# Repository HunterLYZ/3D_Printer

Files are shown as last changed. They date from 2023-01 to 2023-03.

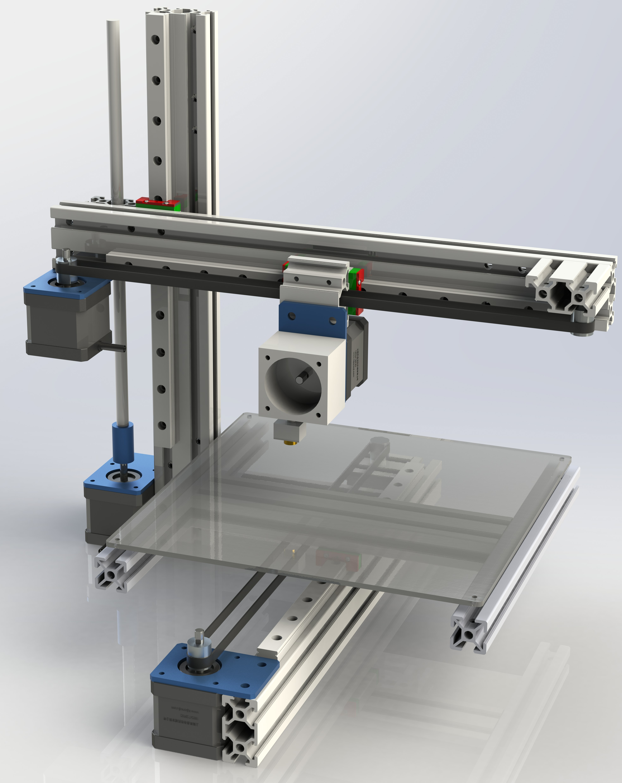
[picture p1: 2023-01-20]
images/1.JPG

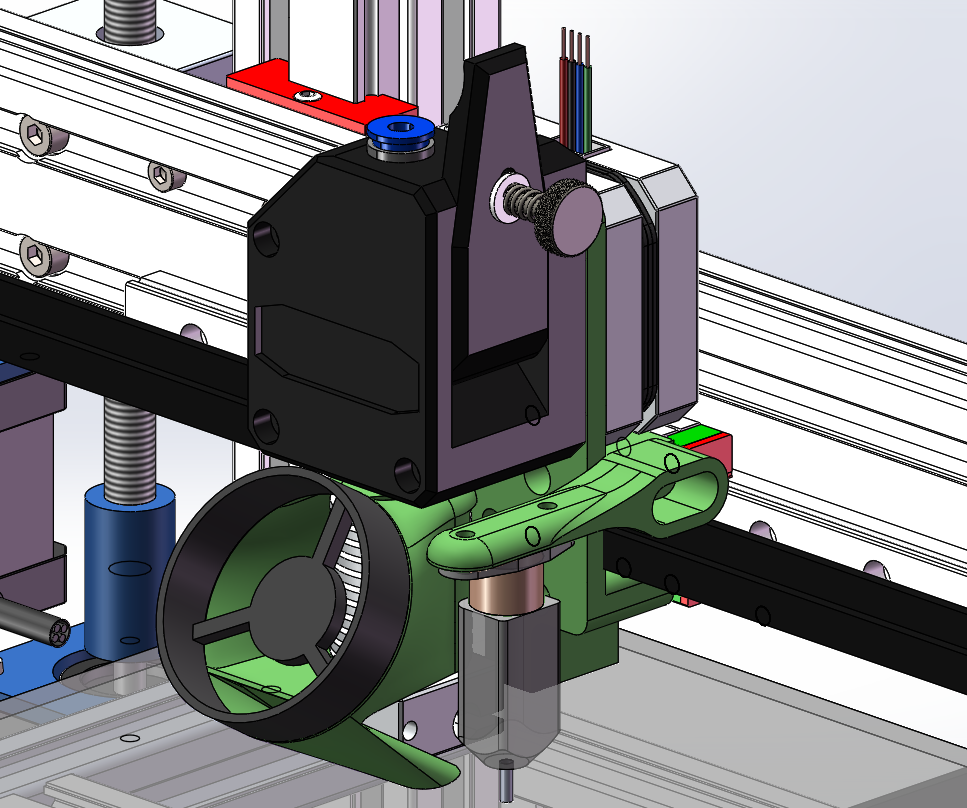
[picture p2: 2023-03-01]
3dtouch BedLeveling/屏幕截图 2023-03-01 191434.png

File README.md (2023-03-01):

# 3D_Printer

Mostly Aluminum Extrusion 3D Printer without printed part and laser cut；

Aim to use the simplest parts to create a low cost 3D printer！

Video description：【DIY悬臂3D打印机，低成本全金属方案开源】 https://www.bilibili.com/video/BV1WG4y1X7HM/?share_source=copy_web&vd_source=848a0bdee68da7365b0da106937491c6
fullview

A simple fan duct for better overhangs：

https://www.thingiverse.com/thing:5817219

屏幕截图 2023-03-01 191434

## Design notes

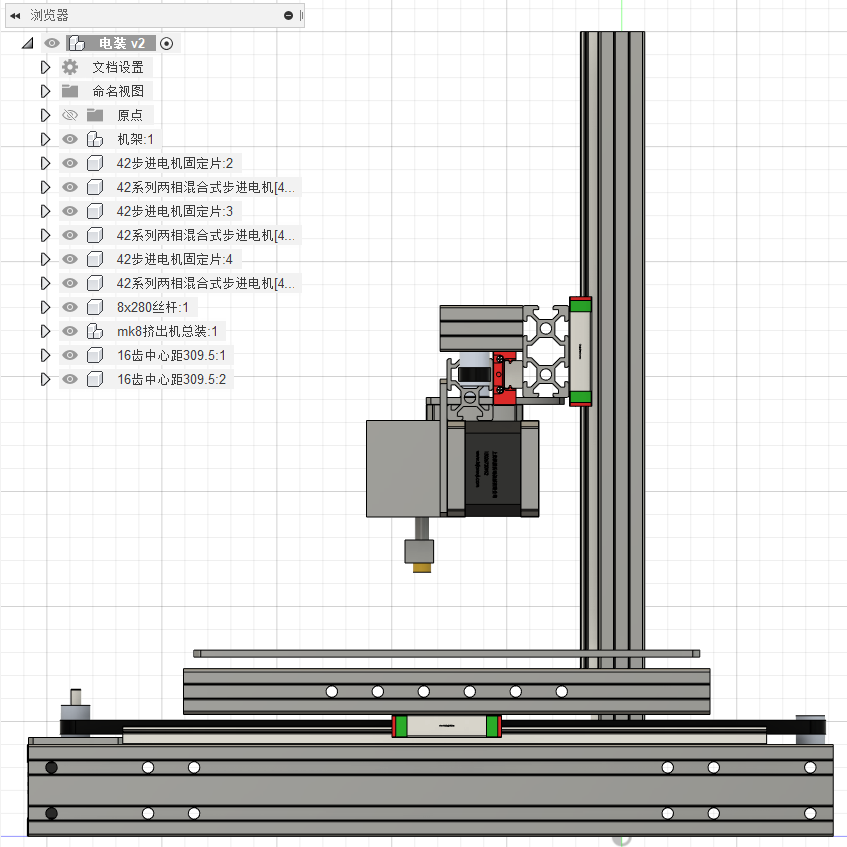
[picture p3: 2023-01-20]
images/右.png

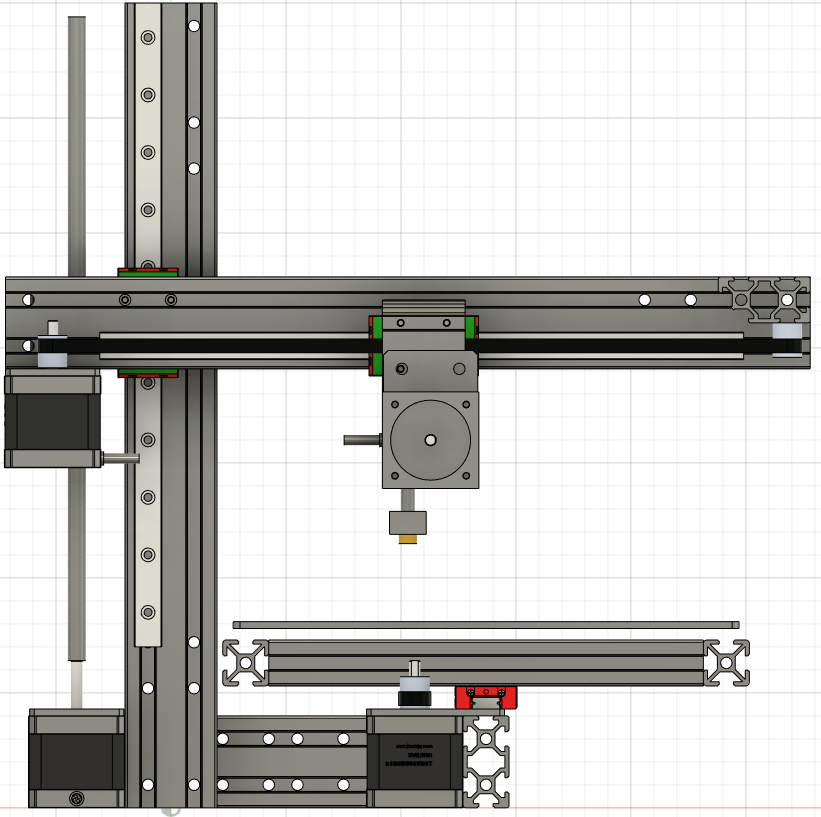
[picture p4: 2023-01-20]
images/前.png

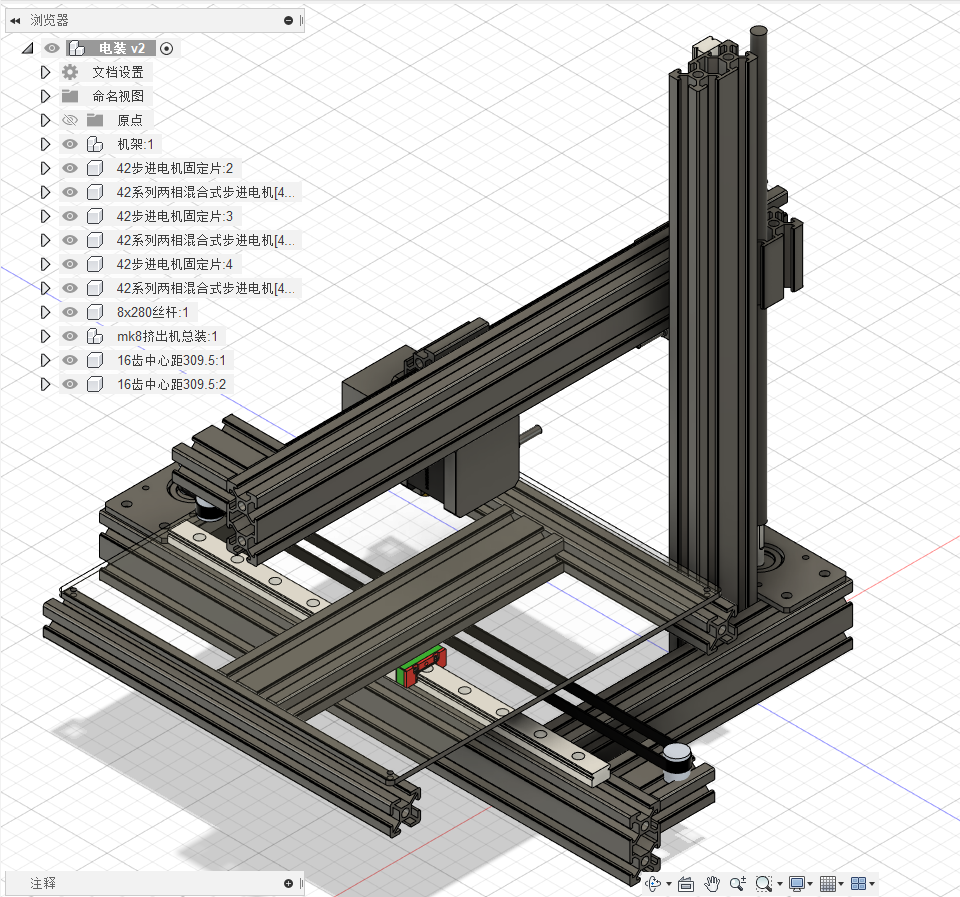
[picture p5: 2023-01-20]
images/侧后.png

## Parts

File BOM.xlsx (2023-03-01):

序号 |  | 名称 | 规格 | 数量 | 单价 | 运费 | 总价 | 链接 | 备注
 | 线轨 | 线轨 | 270mm长轨道+12H滑块（轻预压） | 3 | 30 | 10 | 100 | 闲鱼拆机线轨 | 除非有相关经验，否则建议买新的
 | 铝型材 | 欧标2040V 铝型材 | 360mm长 参照图纸加工 | 2 | 9.83 | 12 | 31.66 | TDT欧标铝型材2020拼装diy框架工作台配件工业框架2020铝合金型材-淘宝网 (taobao.com) (https://item.taobao.com/item.htm?spm=a1z1r.7974869.0.0.269c3ad4cUHl1e&id=610844048816)
 |  |  | 189mm长 参照图纸加工 | 2 | 5.15 | 0 | 10.3
 |  |  | 380mm长 无需加工 | 1 | 10.37 | 0 | 10.37
 |  |  | 40mm长 参照图纸加工 | 3 | 1.07 | 0 | 3.21
 |  | 欧标2020 铝型材 | 228.5mm长 无需加工 | 2 | 3.36 | 0 | 6.72
 | 步进电机 | 挤出机步进电机 | 带1米XH2.54配线高23mm | 1 | 11.4 | 0 | 11.4 | 3D打印机配件42步进电机泰坦挤出机电机小型微型写字机雕刻机马达-淘宝网 (taobao.com) (https://item.taobao.com/item.htm?spm=a1z09.2.0.0.7cb62e8dnEPceC&id=669131789105&_u=1208rr7usgf1c7) | 挤出机用，不超过28mm
 |  | 步进电机 | 40mm高 | 3 | 18 | 6 | 60 | 项目剩余，仅估价
 |  | 42步进电机固定片 | 银色*2；黑色*2共4个 | 4 | 3 | 0 | 12 | 3D打印机配件 42步进电机固定片 安装支架 适用2020 2040铝型材-淘宝网 (taobao.com) (https://item.taobao.com/item.htm?spm=a1z09.2.0.0.7cb62e8dnEPceC&id=595525201976&_u=1208rr7usge8b5)
 |  | 电机线 | 双头白色段子（500mm） | 1 | 0.7 | 0 | 0.7 | XH2.54端子电机线 杜邦头 3D打印机配件 步进电机链接线4pin-6pin-淘宝网 (taobao.com) (https://item.taobao.com/item.htm?spm=a1z10.3-c-s.w4002-17331600343.27.22cc3e69DtHcDt&id=560493265538)
 |  |  | 双头白色段子（800mm） | 1 | 0.9 | 0 | 0.9
 |  |  | 双头白色段子（1000mm） | 1 | 1.1 | 0 | 1.1
 | 同步带轮 | 同步轮 | 20齿内孔5带宽6 | 2 | 1.18 | 0 | 2.36 | 3D打印机2GT同步轮 16/20/40齿传动皮带轮步进电机主动轮带宽6/10-淘宝网 (taobao.com) (https://item.taobao.com/item.htm?spm=a1z10.3-c-s.w4002-17331600343.12.72ce3e69ifWSzl&id=559194333476)
 |  | 惰轮 | 20齿内孔3 带宽6带齿 | 2 | 2.03 | 0 | 4.06 | 3D打印机2GT惰轮 同步带惰轮皮带轮H型被动滑轮16/20齿带宽6/10mm-淘宝网 (taobao.com) (https://item.taobao.com/item.htm?spm=a1z0d.6639537/tb.1997196601.4.631b7484anwYdu&id=559682437946)
 |  | 同步带 | GT2-6mm 1米 | 2 | 1.35 | 0 | 2.7 | 3D打印机2GT同步带 高品质橡胶PU钢丝 GT2传动开口皮带带宽6/10mm-淘宝网 (taobao.com) (https://item.taobao.com/item.htm?spm=a1z10.3-c-s.w4002-17331600343.17.22cc3e69DtHcDt&id=558903222636)
 |  | 同步带固定片 | 夹压带铝齿片 9*40mm | 1 | 0.7 | 0 | 0.7 | Reprap 3D打印机 同步带固定片夹压带铝齿片 9*40mm 氧化处理-淘宝网 (taobao.com) (https://item.taobao.com/item.htm?spm=a1z10.3-c-s.w4002-17331600343.31.22cc3e69DtHcDt&id=560377410082)
 | 热床 | 铝基板热床 | 220*220 | 1 | 25 | 0 | 25 | 3D打印机热床 MK3铝基板热床平台 加热床 reprap标准 220*220*3mm-淘宝网 (taobao.com) (https://item.taobao.com/item.htm?id=561067851671)
 |  | 钢化玻璃板 | 220*220 | 1 | 10.3 | 0 | 10.3 | 3D打印机配件 MK2B加热热床玻璃平台高硼硅钢化玻璃板213x200x3mm-淘宝网 (taobao.com) (https://item.taobao.com/item.htm?spm=a1z10.3-c-s.w4002-17331600343.9.650e3e69Mw5PF8&id=556801926773)
 |  | 热床弹簧 | 挤出机强力弹簧 | 4 | 0.1 | 0 | 0.4 | 同拓3D打印机配件 挤出机强力弹簧 镀镍 wade/Ultimaker /Makerb-淘宝网 (taobao.com) (https://item.taobao.com/item.htm?spm=a1z10.3-c-s.w4002-17331600343.18.7d463e693q8sTS&id=559979934625)
 |  | 晶格玻璃夹 |  | 4 | 0.85 | 0 | 3.4 | 3d打印机晶格玻璃夹 不锈钢热床固定夹子Ender 3同款 可夹7mm-淘宝网 (taobao.com) (https://item.taobao.com/item.htm?spm=a1z10.3-c-s.w4002-17331600343.13.58433e69OT4IVv&id=643012602050)
 |  | NTC热敏电阻 | 银色一支 | 1 | 0.5 | 0 | 0.5 | 3D打印机 NTC热敏电阻 100K/100欧姆 配MK2a 1%高精度 传感器-淘宝网 (taobao.com) (https://item.taobao.com/item.htm?spm=a1z10.3-c-s.w4002-17331600343.45.4a173e69rOCZgU&id=560081231115)
 |  | 固体胶棒 |  | 1 | 2.2 | 0 | 2.2 | 3D打印机配件固体胶棒 防翘边固体胶水溶性PVP胶棒冷打防翘边胶棒-淘宝网 (taobao.com) (https://item.taobao.com/item.htm?spm=a230r.1.14.16.6d2f24e0IERJIc&id=648496928113&ns=1&abbucket=20)
 | 打印头 | 测温电阻NTC100K | 高温版350° | 1 | 2.1 | 0 | 2.1 | 同拓3D打印机测温电阻NTC100K热敏电阻传感器配件热头高温版350度-淘宝网 (taobao.com) (https://item.taobao.com/item.htm?spm=a1z10.3-c-s.w4002-17331600343.51.6fd93e69hTs6JR&id=575202356478)
 |  | 加热棒 | 12V60W 一米 | 1 | 7.5 | 0 | 7.5 | 高品质3D打印机 E3DV6挤出头热端加热棒6*20mm12V/24V 70W加热管-淘宝网 (taobao.com) (https://item.taobao.com/item.htm?spm=a1z10.3-c-s.w4002-17331600343.29.12a93e693xUKBs&id=680484241425)
 |  | 加热块 | 兼容pt1000 | 1 | 1.35 | 0 | 1.35 | 3D打印机配件 新款E3D-V6加热块 硅胶套 兼容PT100传感器加热铝块-淘宝网 (taobao.com) (https://item.taobao.com/item.htm?spm=a1z10.3-c-s.w4002-17331600343.17.6fd93e69hTs6JR&id=565058815432)
 |  | 喷嘴 | 0.4mm | 2 | 0.05 | 0 | 0.1 | 3D打印机喷头 E3D喷嘴V5V6 MK8黄铜带刻字 1.75/3.0耗材 M6螺纹-淘宝网 (taobao.com) (https://item.taobao.com/item.htm?spm=a1z10.3-c-s.w4002-17331600343.14.72ce3e69ifWSzl&id=559468438120)
 |  | 喉管 | TC4钛合金 | 1 | 5.65 | 0 | 5.65 | 3d打印机钛合金喉管e3d V6远程 TC4钛合金耐磨耐腐蚀高温耗材专用-淘宝网 (taobao.com) (https://item.taobao.com/item.htm?spm=a1z10.3-c-s.w4002-17331600343.36.6ee13e69zr7aBP&id=635261524077)
 |  | 散热管 | V6远程通用M7喉管 | 1 | 3.2 | 0 | 3.2 | 3d打印机配件 J-head散热管 E3D-V5 V6远程近程散热器片 1.75/3mm-淘宝网 (taobao.com) (https://item.taobao.com/item.htm?spm=a1z10.3-c-s.w4002-17331600343.47.50f73e69FBJrfH&id=559984859809)
 |  | 风扇 | v6风扇罩+12v风扇 | 1 | 4.8 | 0 | 4.8 | 3d打印机风扇罩 E3D V5 V6专用注塑散热器风扇支架固定座 30*30-淘宝网 (taobao.com) (https://item.taobao.com/item.htm?spm=a1z09.2.0.0.7cb62e8dnEPceC&id=559908577688&_u=1208rr7usgd1f7)
 | 挤出机 | 四氟管 | 2*4mm | 1 | 2 | 0 | 2 | 铁氟龙管聚四氟乙烯四氟管特氟龙PTFE软管耐腐蚀高温送料管导料管-淘宝网 (taobao.com) (https://item.taobao.com/item.htm?spm=a1z10.3-c-s.w4002-17331600343.35.11473e69qQkCo4&id=659862681620)
 |  | BMG挤出机 | 透明款 | 1 | 22 | 0 | 22 | 3D打印机配件 新款BMG透明挤出机 双齿轮减速 软性耗材远近程可用-淘宝网 (taobao.com) (https://item.taobao.com/item.htm?spm=a1z10.3-c-s.w4002-17331600343.31.749a3e69Eeaqys&id=640392766176)
 | 主板 | 2004显示屏 |  | 1 | 28 | 0 | 28 | 3d打印机显示屏模块 1.4主板智能控制器 LCD 2004 12864液晶屏-淘宝网 (taobao.com) (https://item.taobao.com/item.htm?spm=a1z10.3-c-s.w4002-17331600343.31.424a3e69WKIBUf&id=617517153780) | 主板老旧，建议选用流行型号
 |  | Reprap Ramps 1.4 控制板 |  | 1 | 12 | 0 | 12 | 3D打印机 Reprap Ramps 1.4 控制板 扩展板 MendelPrusa-淘宝网 (taobao.com) (https://item.taobao.com/item.htm?spm=a230r.1.14.43.4a5876b5RmAauQ&id=573082984050&ns=1&abbucket=20)
 |  | MEGA2560 R3开发板 | ch340串口芯片 | 1 | 62.8 | 0 | 62.8 | 新版MEGA2560 R3开发板 改进版ATMEGA16U2 CH340 兼容Arduino-tmall.com天猫 (https://detail.tmall.com/item.htm?abbucket=20&id=675919562593&ns=1&spm=a230r.1.14.23.74898474FCToI7)
 |  | TMC2208 |  | 4 | 8.19 | 3 | 35.76 | 3D打印机配件 TMC2208 V1.2升级版步进电机静音驱动器模块256细分-淘宝网 (taobao.com) (https://item.taobao.com/item.htm?spm=a1z0d.7625083.1998302264.6.5c5f4e69R3AJB0&id=677318046407)
 | 杂项 | 开关电源 | 12v20a | 1 | 35 | 0 | 35 | 220V转变5V12V24V直流开关电源3a5a10a监控变压器LED灯带条电源伏-淘宝网 (taobao.com) (https://item.taobao.com/item.htm?spm=a1z09.2.0.0.6ffa2e8dR5PuxG&id=595783963500&_u=s208d75pet6ef6)
 |  | 限位开关 | 自己焊线 | 3 | 0.3 | 0 | 0.9 | 同拓3D打印机配件Makerbot MK7/MK8原点限位轻触行程开关1A直角-淘宝网 (taobao.com) (https://item.taobao.com/item.htm?spm=a1z0d.6639537/tb.1997196601.4.1cbb7484JUjzla&id=560293912375)
 |  | T8丝杆 | 300mm配螺母 | 1 | 8.2 | 0 | 8.2 | T型T8步进电机丝杆3D打印机梯形丝杆300mm套装配螺母导程2MM直径8-淘宝网 (taobao.com) (https://item.taobao.com/item.htm?spm=a1z10.3-c-s.w4002-17331600343.51.69b33e69VoroIb&id=575727966830)
 |  | 联轴器 | 5*8 | 1 | 0.9 | 0 | 0.9 | 3D打印机配件 刚性联轴器 铝合金电机船模车模航模连轴器小5*8mm-淘宝网 (taobao.com) (https://item.taobao.com/item.htm?spm=a1z10.3-c-s.w4002-17331600343.25.69b33e69VoroIb&id=559746722650)
 |  | 耐高温硅胶线14awg | 红黑各一米 | 2 | 2.8 | 0 | 5.6 | 超软耐高温硅胶线16 14 12 10 8 7 6AWG平方航模新能源汽车锂电池-淘宝网 (taobao.com) (https://item.taobao.com/item.htm?spm=a230r.1.14.22.6dfb5430QOtYIL&id=654286714565&ns=1&abbucket=20)
 |  | 耐高温硅胶线22awg | 红黑各两米 | 4 | 1 | 0 | 4
 | 螺丝螺母 | 沉头螺钉 | M3×40 | 4 | 0.5 | 0 | 2 | 304不锈钢螺丝大全 十字沉头机丝螺栓螺钉KM平头螺丝钉M2M3M4M5M6-淘宝网 (taobao.com) (https://item.taobao.com/item.htm?spm=a1z10.3-c.w4002-23012147333.12.397ad395PYheml&id=40328525933) | 固定热床
 |  | 圆头内六角螺丝 | M3×16 | 50 | 0.04 | 0 | 2 | 304不锈钢圆头内六角螺丝钉盘头螺栓半圆杯蘑菇螺钉M3M4M5M6M8M10-淘宝网 (taobao.com) (https://item.taobao.com/item.htm?spm=a1z09.2.0.0.67002e8dehNNoQ&id=594352604482&_u=1208rr7usg479f) | 固定型材与滑块
 |  |  | M3×8 | 50 | 0.04 | 0 | 2 |  | 用于固定线轨、T型螺母
 |  |  | M3×45 | 20 | 0.14 | 0 | 2.8 |  | 固定惰轮
 |  |  | M5×8 | 10 | 0.21 | 0 | 2.1 |  | 固定电机与型材
 |  |  | M5×18 | 10 | 0.29 | 0 | 2.9 |  | 固定型材与型材
 |  |  | M5×22 | 10 | 0.3 | 0 | 3 |  | 固定惰轮，固定y轴皮带
 |  | 滑块螺母 | 欧标型材T型螺母t型滑块M3 | 50 | 0.094 | 0 | 4.7 | 欧标型材T型螺母t型滑块方形20型30型40型45型-M3-M4-M5-M6-M8-M-淘宝网 (taobao.com) (https://item.taobao.com/item.htm?spm=a1z09.2.0.0.67002e8dehNNoQ&id=654438908453&_u=1208rr7usgf7f7)
 |  |  | 欧标型材T型螺母t型滑块M5 | 50 | 0.09 | 0 | 4.5
 |  | 角码 | 36*16*2 | 5 | 0.418 | 0 | 2.09 | 同拓 不锈钢直片一字角码连接固定件家具椅子床加固铁片五金配件-淘宝网 (taobao.com) (https://item.taobao.com/item.htm?spm=a1z10.3-c-s.w4002-17331600343.56.12ba3e69El2TmH&id=610333007663)
 |  |  |  |  |  | 合计: | 569.93 | 如有遗漏或错误，麻烦您联系我更正，谢谢
 |  |  |  |  |  |  |  | https://github.com/HunterLYZ/3D_Printer
 |  |  |  |  |  |  |  | DIY悬臂3D打印机，低成本全金属方案开源_哔哩哔哩_bilibili (https://www.bilibili.com/video/BV1WG4y1X7HM/?spm_id_from=333.999.0.0)
 |  |  |  |  |  |  |  | liuyunzhe2002@outlook.com
 |  |  |  |  |  |  |  | 2023/3/1更新

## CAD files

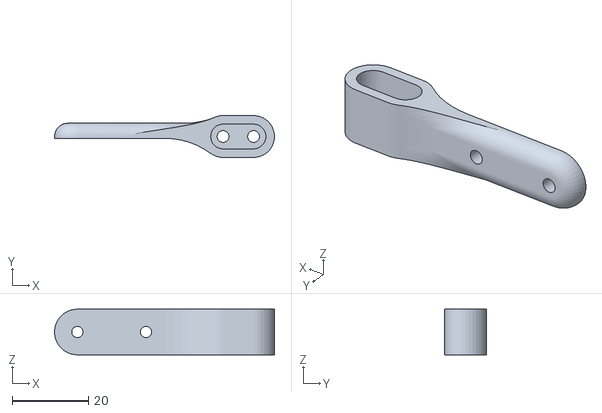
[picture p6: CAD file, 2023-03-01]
3dtouch BedLeveling/3DtouchCarr.STL
57.8 x 11.0 x 12.0

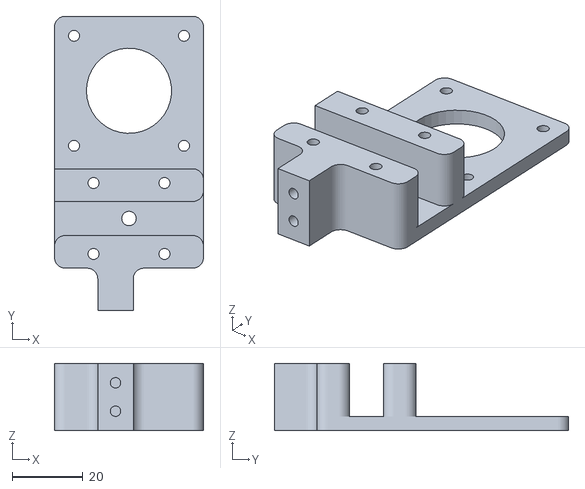
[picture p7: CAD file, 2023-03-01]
3dtouch BedLeveling/printheadHolder.STL
42.0 x 83.0 x 19.0

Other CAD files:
Aluminum Extrusion/铝型材加工v3.dxf

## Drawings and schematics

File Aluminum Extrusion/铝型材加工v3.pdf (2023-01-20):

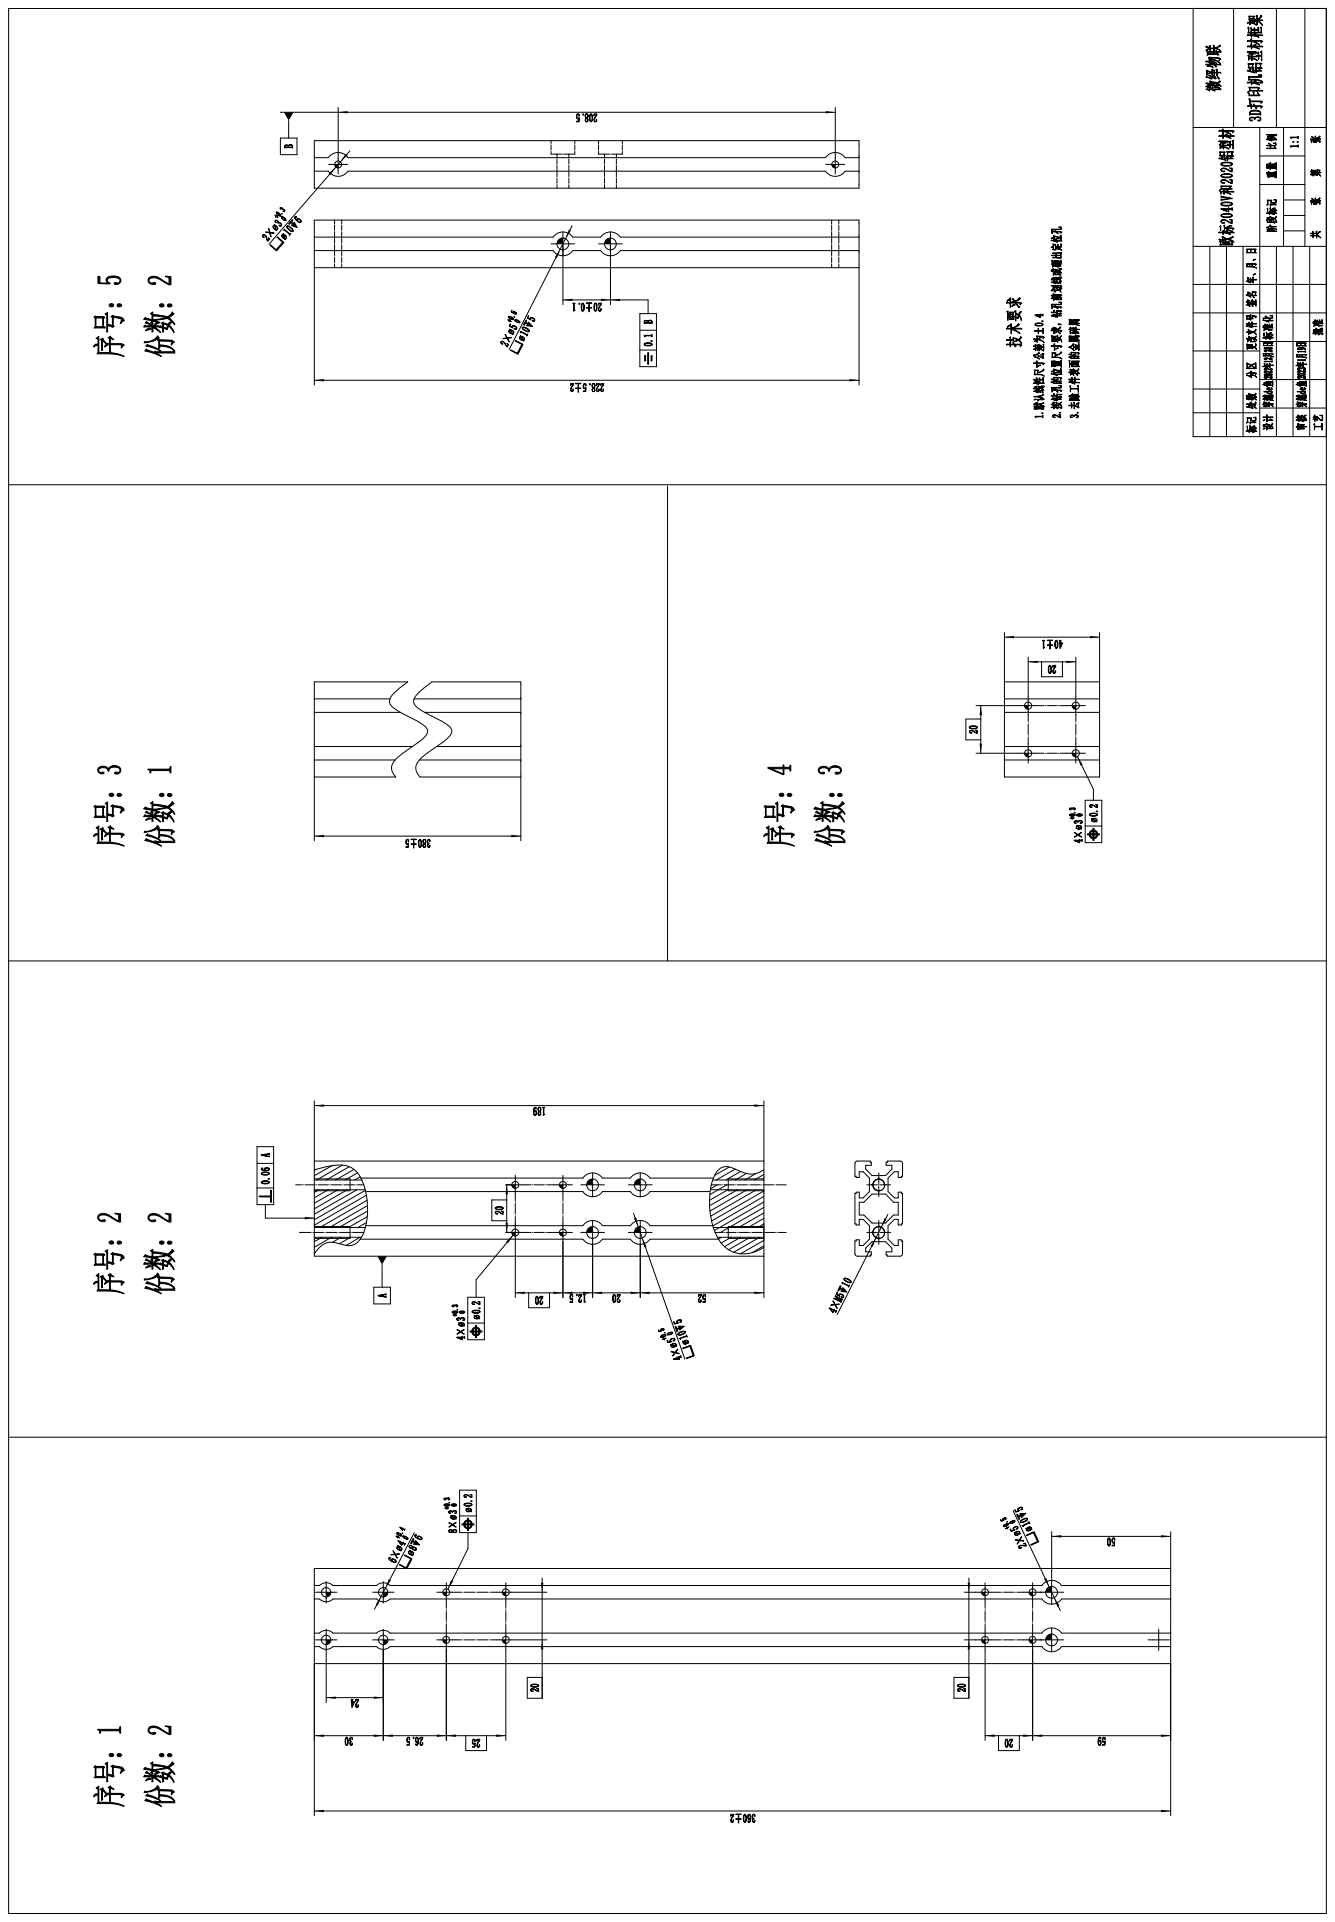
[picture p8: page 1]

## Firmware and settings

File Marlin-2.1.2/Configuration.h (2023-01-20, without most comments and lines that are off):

#pragma once
#define CONFIGURATION_H_VERSION 02010200
#define STRING_CONFIG_H_AUTHOR "(HunterL, custom config)" // Who made the changes.
#define SHOW_BOOTSCREEN
  #define MOTHERBOARD BOARD_RAMPS_14_EFB
#define SERIAL_PORT 0
#define BAUDRATE 250000
#define X_DRIVER_TYPE  A4988
#define Y_DRIVER_TYPE  A4988
#define Z_DRIVER_TYPE  A4988
#define E0_DRIVER_TYPE A4988
#define EXTRUDERS 1
#define DEFAULT_NOMINAL_FILAMENT_DIA 1.75
#define TEMP_SENSOR_0 1
#define TEMP_SENSOR_1 0
#define TEMP_SENSOR_2 0
#define TEMP_SENSOR_3 0
#define TEMP_SENSOR_4 0
#define TEMP_SENSOR_5 0
#define TEMP_SENSOR_6 0
#define TEMP_SENSOR_7 0
#define TEMP_SENSOR_BED 1
#define TEMP_SENSOR_PROBE 0
#define TEMP_SENSOR_CHAMBER 0
#define TEMP_SENSOR_COOLER 0
#define TEMP_SENSOR_BOARD 0
#define TEMP_SENSOR_REDUNDANT 0
#define DUMMY_THERMISTOR_998_VALUE  25
#define DUMMY_THERMISTOR_999_VALUE 100
#if TEMP_SENSOR_IS_MAX_TC(0)
  #define MAX31865_SENSOR_OHMS_0      100 // (Ω) Typically 100 or 1000 (PT100 or PT1000)
  #define MAX31865_CALIBRATION_OHMS_0 430 // (Ω) Typically 430 for Adafruit PT100; 4300 for Adafruit PT1000
#endif
#if TEMP_SENSOR_IS_MAX_TC(1)
  #define MAX31865_SENSOR_OHMS_1      100
  #define MAX31865_CALIBRATION_OHMS_1 430
#endif
#if TEMP_SENSOR_IS_MAX_TC(2)
  #define MAX31865_SENSOR_OHMS_2      100
  #define MAX31865_CALIBRATION_OHMS_2 430
#endif
#if HAS_E_TEMP_SENSOR
  #define TEMP_RESIDENCY_TIME         10  // (seconds) Time to wait for hotend to "settle" in M109
  #define TEMP_WINDOW                  1  // (°C) Temperature proximity for the "temperature reached" timer
  #define TEMP_HYSTERESIS              3  // (°C) Temperature proximity considered "close enough" to the target
#endif
#if TEMP_SENSOR_BED
  #define TEMP_BED_RESIDENCY_TIME     10  // (seconds) Time to wait for bed to "settle" in M190
  #define TEMP_BED_WINDOW              1  // (°C) Temperature proximity for the "temperature reached" timer
  #define TEMP_BED_HYSTERESIS          3  // (°C) Temperature proximity considered "close enough" to the target
#endif
#if TEMP_SENSOR_CHAMBER
  #define TEMP_CHAMBER_RESIDENCY_TIME 10  // (seconds) Time to wait for chamber to "settle" in M191
  #define TEMP_CHAMBER_WINDOW          1  // (°C) Temperature proximity for the "temperature reached" timer
  #define TEMP_CHAMBER_HYSTERESIS      3  // (°C) Temperature proximity considered "close enough" to the target
#endif
#if TEMP_SENSOR_REDUNDANT
  #define TEMP_SENSOR_REDUNDANT_SOURCE    E1  // The sensor that will provide the redundant reading.
  #define TEMP_SENSOR_REDUNDANT_TARGET    E0  // The sensor that we are providing a redundant reading for.
  #define TEMP_SENSOR_REDUNDANT_MAX_DIFF  10  // (°C) Temperature difference that will trigger a print abort.
#endif
#define HEATER_0_MINTEMP   5
#define HEATER_1_MINTEMP   5
#define HEATER_2_MINTEMP   5
#define HEATER_3_MINTEMP   5
#define HEATER_4_MINTEMP   5
#define HEATER_5_MINTEMP   5
#define HEATER_6_MINTEMP   5
#define HEATER_7_MINTEMP   5
#define BED_MINTEMP        5
#define CHAMBER_MINTEMP    5
#define HEATER_0_MAXTEMP 275
#define HEATER_1_MAXTEMP 275
#define HEATER_2_MAXTEMP 275
#define HEATER_3_MAXTEMP 275
#define HEATER_4_MAXTEMP 275
#define HEATER_5_MAXTEMP 275
#define HEATER_6_MAXTEMP 275
#define HEATER_7_MAXTEMP 275
#define BED_MAXTEMP      150
#define CHAMBER_MAXTEMP  60
#define HOTEND_OVERSHOOT 15   // (°C) Forbid temperatures over MAXTEMP - OVERSHOOT
#define BED_OVERSHOOT    10   // (°C) Forbid temperatures over MAXTEMP - OVERSHOOT
#define COOLER_OVERSHOOT  2   // (°C) Forbid temperatures closer than OVERSHOOT
#define PIDTEMP          // See the PID Tuning Guide at https://reprap.org/wiki/PID_Tuning
#define BANG_MAX 255     // Limits current to nozzle while in bang-bang mode; 255=full current
#define PID_MAX BANG_MAX // Limits current to nozzle while PID is active (see PID_FUNCTIONAL_RANGE below); 255=full current
#define PID_K1 0.95      // Smoothing factor within any PID loop
    #define DEFAULT_Kp  22.20
    #define DEFAULT_Ki   1.08
    #define DEFAULT_Kd 114.00
#define MAX_BED_POWER 255 // limits duty cycle to bed; 255=full current
#define MAX_CHAMBER_POWER 255 // limits duty cycle to chamber heater; 255=full current
  #define PID_FUNCTIONAL_RANGE 10 // If the temperature difference between the target temperature and the actual temperature
#define PREVENT_COLD_EXTRUSION
#define EXTRUDE_MINTEMP 170
#define PREVENT_LENGTHY_EXTRUDE
#define EXTRUDE_MAXLENGTH 200
#define THERMAL_PROTECTION_HOTENDS // Enable thermal protection for all extruders
#define THERMAL_PROTECTION_BED     // Enable thermal protection for the heated bed
#define THERMAL_PROTECTION_CHAMBER // Enable thermal protection for the heated chamber
#define THERMAL_PROTECTION_COOLER  // Enable thermal protection for the laser cooling
#define USE_XMIN_PLUG
#define USE_YMIN_PLUG
#define USE_ZMIN_PLUG
#define ENDSTOPPULLUPS
#define X_MIN_ENDSTOP_INVERTING false // Set to true to invert the logic of the endstop.
#define Y_MIN_ENDSTOP_INVERTING false // Set to true to invert the logic of the endstop.
#define Z_MIN_ENDSTOP_INVERTING false // Set to true to invert the logic of the endstop.
#define I_MIN_ENDSTOP_INVERTING false // Set to true to invert the logic of the endstop.
#define J_MIN_ENDSTOP_INVERTING false // Set to true to invert the logic of the endstop.
#define K_MIN_ENDSTOP_INVERTING false // Set to true to invert the logic of the endstop.
#define U_MIN_ENDSTOP_INVERTING false // Set to true to invert the logic of the endstop.
#define V_MIN_ENDSTOP_INVERTING false // Set to true to invert the logic of the endstop.
#define W_MIN_ENDSTOP_INVERTING false // Set to true to invert the logic of the endstop.
#define X_MAX_ENDSTOP_INVERTING false // Set to true to invert the logic of the endstop.
#define Y_MAX_ENDSTOP_INVERTING false // Set to true to invert the logic of the endstop.
#define Z_MAX_ENDSTOP_INVERTING false // Set to true to invert the logic of the endstop.
#define I_MAX_ENDSTOP_INVERTING false // Set to true to invert the logic of the endstop.
#define J_MAX_ENDSTOP_INVERTING false // Set to true to invert the logic of the endstop.
#define K_MAX_ENDSTOP_INVERTING false // Set to true to invert the logic of the endstop.
#define U_MAX_ENDSTOP_INVERTING false // Set to true to invert the logic of the endstop.
#define V_MAX_ENDSTOP_INVERTING false // Set to true to invert the logic of the endstop.
#define W_MAX_ENDSTOP_INVERTING false // Set to true to invert the logic of the endstop.
#define Z_MIN_PROBE_ENDSTOP_INVERTING false // Set to true to invert the logic of the probe.
#define DEFAULT_AXIS_STEPS_PER_UNIT   { 80, 80, 400, 415 }
#define DEFAULT_MAX_FEEDRATE          { 120, 90, 10, 25 }
#define DEFAULT_MAX_ACCELERATION      { 2400, 1600, 100, 8000 }
#define DEFAULT_ACCELERATION          1200    // X, Y, Z and E acceleration for printing moves
#define DEFAULT_RETRACT_ACCELERATION  800    // E acceleration for retracts
#define DEFAULT_TRAVEL_ACCELERATION   800    // X, Y, Z acceleration for travel (non printing) moves
#define DEFAULT_EJERK    5.0  // May be used by Linear Advance
  #define JUNCTION_DEVIATION_MM 0.013 // (mm) Distance from real junction edge
  #define JD_HANDLE_SMALL_SEGMENTS    // Use curvature estimation instead of just the junction angle
#define Z_MIN_PROBE_USES_Z_MIN_ENDSTOP_PIN
#define NOZZLE_TO_PROBE_OFFSET { 10, 10, 0 }
#define PROBING_MARGIN 10
#define XY_PROBE_FEEDRATE (133*60)
#define Z_PROBE_FEEDRATE_FAST (4*60)
#define Z_PROBE_FEEDRATE_SLOW (Z_PROBE_FEEDRATE_FAST / 2)
#define Z_CLEARANCE_DEPLOY_PROBE   10 // Z Clearance for Deploy/Stow
#define Z_CLEARANCE_BETWEEN_PROBES  5 // Z Clearance between probe points
#define Z_CLEARANCE_MULTI_PROBE     5 // Z Clearance between multiple probes
#define Z_PROBE_LOW_POINT          -2 // Farthest distance below the trigger-point to go before stopping
#define Z_PROBE_OFFSET_RANGE_MIN -20
#define Z_PROBE_OFFSET_RANGE_MAX 20
#define X_ENABLE_ON 0
#define Y_ENABLE_ON 0
#define Z_ENABLE_ON 0
#define E_ENABLE_ON 0 // For all extruders
#define DISABLE_X false
#define DISABLE_Y false
#define DISABLE_Z false
#define DISABLE_E false             // Disable the extruder when not stepping
#define DISABLE_INACTIVE_EXTRUDER   // Keep only the active extruder enabled
#define INVERT_X_DIR false
#define INVERT_Y_DIR true
#define INVERT_Z_DIR false
#define INVERT_E0_DIR false
#define INVERT_E1_DIR false
#define INVERT_E2_DIR false
#define INVERT_E3_DIR false
#define INVERT_E4_DIR false
#define INVERT_E5_DIR false
#define INVERT_E6_DIR false
#define INVERT_E7_DIR false
#define X_HOME_DIR -1
#define Y_HOME_DIR -1
#define Z_HOME_DIR -1
#define X_BED_SIZE 200
#define Y_BED_SIZE 200
#define X_MIN_POS -15
#define Y_MIN_POS -15
#define Z_MIN_POS -3
#define X_MAX_POS X_BED_SIZE
#define Y_MAX_POS Y_BED_SIZE
#define Z_MAX_POS 180
#define MIN_SOFTWARE_ENDSTOPS
  #define MIN_SOFTWARE_ENDSTOP_X
  #define MIN_SOFTWARE_ENDSTOP_Y
  #define MIN_SOFTWARE_ENDSTOP_Z
  #define MIN_SOFTWARE_ENDSTOP_I
  #define MIN_SOFTWARE_ENDSTOP_J
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

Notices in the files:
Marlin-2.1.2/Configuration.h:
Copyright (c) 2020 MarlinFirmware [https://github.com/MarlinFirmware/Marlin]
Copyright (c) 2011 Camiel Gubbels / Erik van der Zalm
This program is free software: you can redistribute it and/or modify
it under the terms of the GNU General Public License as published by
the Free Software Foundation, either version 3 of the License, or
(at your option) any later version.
